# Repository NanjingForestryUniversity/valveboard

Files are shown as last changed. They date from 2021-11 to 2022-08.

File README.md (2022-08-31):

# 阀板

阀板接收上位机给的数据，按其要求控制高速喷阀的开启和关闭，用在棉花、烟叶、茶叶等分选机上，喷阀多用来吹走其中的杂质。因此阀板是分选步骤上控制最终执行机构的驱动板，要求高速、稳定。**这个文件夹下为烟梗分选机阀板相关内容。**

## 目录结构

- 硬件上阀板就是控制喷阀的板子，相关原理图、PCB、BOM、硬件说明等在`hardware`目录里

- 阀板仅驱动喷阀，具体哪个开启哪个关闭要遵循上级的指令，指令传输过程须符合通信协议，通信协议在`protocol`目录里

- 阀板读取通信数据、发出控制信号的操作由阀板上的CPLD进行，其固件和说明见`firmware`目录
- 另外提供了若干输出符合阀板通信协议的信号的例子，在`examples`目录里，严格上这不属于阀板工程

## 版本

由于阀板经常有不同类型的新要求出现，比如24路阀板、32路阀板、控制不同参数的新阀，因此不同的阀板型号（注意不是更新，比如阀板上添加级联接口属于更新）应建立不同的分支，**[b01-c48-ponlytest-vgeneral](https://github.com/NanjingForestryUniversity/valveboard/tree/b01-c48-ponlytest-vgeneral)分支无实际意义**

分支命名规则（不使用中文，小写无空格）

```shell
b分支编号-c路数-p生产环境项目名-v喷阀信息-[-其他特点1[-其他特点2...]]
```

中括号在这里表示可省略的项，中括号本身不应出现在实际命名中，其他特点应字母打头，可有多个，"-"相连

使用Git的tag功能定义版本（注意连着tag一起push），Github仓库的release功能同步发布最新版本的PCB生产文件、PCB制造视图、BOM表、板载固件、通信协议手册

版本号遵循定义如下（不使用中文，小写无空格）

```shell
b分支编号-h硬件版本-p协议版本-f固件版本
```

分支编号和分支命名中编号一致

##  作者

[过奕任](https://github.com/3703781)、丁坤。老阀板工程很乱，重新开发了关于阀板的一切，并放到这个仓库里，以后就在这个仓库里迭代更新。欢迎提[issue](https://github.com/NanjingForestryUniversity/valveboard/issues)，bug随缘解决。

丁坤2019年入学虽然已经毕业，但也很乐意解答关于阀板的所有问题。丁坤QQ1091546069、丁坤电话17761700156。

过奕任2020年入学，目前正打算找其他人接管这个库，毕业了就不要找他，但永远可以找丁坤。

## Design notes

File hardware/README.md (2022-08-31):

# 阀板硬件

这个文件夹下是48路阀板的原理图和PCB，用于烟梗分选机。整个机器用了六块48路阀板，驱动256路喷嘴，阀的型号是合肥旭伟电子气动有限公司的XW-F16，这个阀一个可以连接并控制16个喷嘴。每个阀的电阻是14欧姆，高压启动时峰值电流约1.5A，低压保持电流约0.8A。

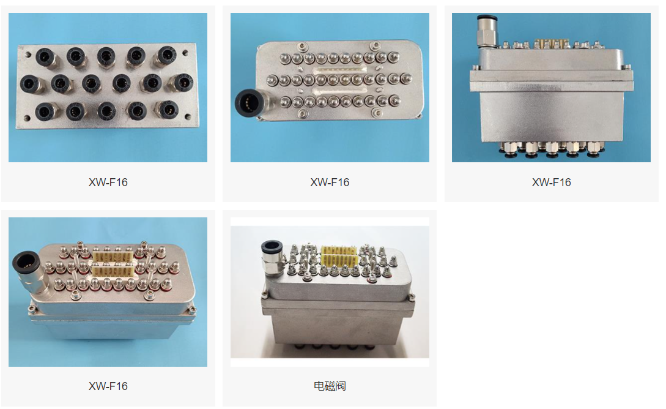
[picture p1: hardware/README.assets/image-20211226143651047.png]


## 概述

48个电磁阀连接在顶部的12个接口上，当接口上有电压时电流流过电磁阀，电磁阀打开。由于电磁阀工作需要大电流大电压且为感性器件，容易影响发出控制信号的CPLD芯片，因此需要独立且隔离的电源，这个电源标为`LOW`，参考为`PGND`。为加快电磁阀开启，在开启瞬间会输出一个高电压，这是另一个独立的电源，标为`HIGH`，参考也为`PGND`。这个高电压会在电磁阀开启后被断开，随后施加标号为`LOW`的保持电压，用来保持电磁阀的打开状态。需要电磁阀关闭则切断保持电压。

上面的过程由光耦隔离驱动端MOS和控制芯片CPLD，提供给光耦输出端的电压标号为`+12V`，参考为`PGND`。

上述提及的`LOW`、`HIGH`、`PGND`、`+12V`仅为板子的丝印上的称呼，都在右上角电源接口输入。

CPLD为控制芯片，接收外部信号并将控制信号输出到板上的光耦，数字电路部分和光耦输入端的电源标号为`DGND`、`+12V`，仅为板子的丝印上的称呼，都在右下角电源接口输入，当然，输入的12V会转换为3.3V提供给数字电路。

设计时是按照下表电压来做的

| 丝印 | 电压 |
| ---- | --- |
| LOW  | 12~24V  |
| HIGH | 24~100V |
| PGND | 0V |
| +12V | 12V |
| DGND | 0V |
| +12V | 12V |

本次所用的阀板加速开启用的高电压为直流100V、保持用的低电压为直流12V

## 调试

**版号**

在`INFO`丝印标志的区域有`S1`、`S2`、`S3`、`S4`标注的0欧电阻焊接位，按`0`、`1`标注焊接即可，注意0和1不能都焊。这个设置是为阀板级联做的冗余。

**烧录**

CPLD烧录口为简牛口，用USB Blaster烧录的，开发软件为Quartus。旁边的按键是复位信号按键，说白了就是复位按键。用`TTL`接口可以方便单端信号的调试

**观察开关量**

在正面那排光耦前有LED，打开的阀门那一路对应的LED亮。选用LED和串联限流电阻时，查看[issue#2](https://github.com/NanjingForestryUniversity/valveboard/issues/2)

**电源**

数字电源输入为12V，在板子上转换为3.3V，网络标号+3.3V，为防止电磁阀上电瞬间直接误动作，因此给光耦电源加入RC延时电路，输出标号为+3.3VGG，按设计延时约500ms，这个时间远大于CPLD初始化开始工作的时间，因此电磁阀上电瞬间不会误动作。此外还添加了防反接保护，查看[issue#3](https://github.com/NanjingForestryUniversity/valveboard/issues/3)

## 生产制造

所需器件BOM里都有，板子开窗部分要加锡，钢网上已经体现了。测试板子是嘉立创做的，SMT也是嘉立创，直插元件和芯片需手焊

## Changelog
### v1.0 

绿色的阀板，测试版本，继承于远古的原理图和布局

### v1.1

蓝色的阀板，过奕任选型和画原理图，丁坤layout，具有ISO、LVDS、TTL接口，见[b01-h1.1-p1.1-f1.1](https://github.com/NanjingForestryUniversity/valveboard/releases/tag/b01-h1.1-p1.1-f1.1)

### v1.2

黄色的阀板，过奕任画原理图和layout，见 [b02-h1.2-p1.1-f1.2](https://github.com/NanjingForestryUniversity/valveboard/releases/tag/b02-h1.2-p1.1-f1.2)

- 采用带屏蔽的超六类RJ45端口代替原来的牛角座，增强了通信的稳定性
- 删除了ISO（隔离）端口
- 删除了LVDS的BYPASS端口
- 删除了TTL端口
- 修改电磁喷阀的接口为更容易买到的器件，[器件详情](https://detail.tmall.com/item.htm?id=633917290163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)
- 增加了光隔数字部分电源的延迟上电电路，避免启动瞬间喷阀动作
- 修改了1N4148的封装为SOD-123，方便SMT
- 略微优化了板子尺寸，调整了安装孔位置和个数

### v1.3

绿色的阀板，过奕任画原理图和layout，见[b02-h1.3-p1.1-f1.3](https://github.com/NanjingForestryUniversity/valveboard/releases/tag/b02-h1.3-p1.1-f1.3)

- 重画了原理图和PCB，PCB尺寸减小
- 增大阻容器件封装，解决100V耐压风险，[issue#1](https://github.com/NanjingForestryUniversity/valveboard/issues/1)
- LED改为黄绿色，[issue#2](https://github.com/NanjingForestryUniversity/valveboard/issues/2)
- 添加了数字电源防反接，[issue#3](https://github.com/NanjingForestryUniversity/valveboard/issues/3)
- 取消了所有保险丝
- 增加了每一路的标识丝印，南林的徽标
- 重新排列了阀的连接器，方便插拔
- 有需要的线路上增加了开窗，提高载流能力

## 作者

[过奕任](https://github.com/3703781)和丁坤一起设计了电路，画了板子。欢迎提[issue](https://github.com/NanjingForestryUniversity/valveboard/issues)，bug随缘解决。

丁坤2019年入学时就被师兄叫去焊接汪学良的阀板，后来和过奕任接替师兄做了这个仓库里的阀板。丁坤已经毕业，但也很乐意解答关于板子的所有问题。丁坤QQ1091546069、丁坤电话17761700156。

过奕任2020年入学，目前正打算找其他人接管这个库，毕业了就不要找他，但永远可以找丁坤。

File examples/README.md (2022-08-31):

# 发送端实现举例

## 概述

按照阀板程序，这里为基于三个平台的发送端实现

- stm32f103

  VScode工程，参考https://github.com/3703781/vstm32code

- zynq7100

  实现了发送模块，可直接例化
  
- epc9600

  基于嵌入式linux的程序，线程安全，具体板子为EPC-9600I-L，是广州致远电子有限公司开发的基于AM335x系列处理器的工控主板，处理器内核为800MHz的Arm Cortex-A8。

##  作者
[过奕任](https://github.com/3703781)、丁坤。欢迎提[issue](https://github.com/NanjingForestryUniversity/valveboard/issues)，bug随缘解决。

过奕任2020年入学，目前正打算找其他人接管这个库，毕业了就不要找他，但永远可以找丁坤。

丁坤2019年入学、丁坤QQ1091546069、丁坤电话17761700156，已经毕业，但很乐意解答所有问题。

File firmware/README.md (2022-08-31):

# 阀板固件

这是阀板上CPLD的固件，严格意义上也属于硬件，因为是描述的硬件结构。这个固件是按照通信协议写的，但比通信协议能适应更广的传输速度，**烟梗分选机上`SCLK`为2MHz，高电平时间为0.2ms**

## 如何烧录

Quartus软件

## 程序说明

看程序注释

## Changelog
### v1.0

继承自老程序

### v1.1

丁坤重写了

### v1.2

修正了引脚分配

### v1.3

- 添加了高电压抑制，见[issue#4](https://github.com/NanjingForestryUniversity/valveboard/issues/4)
- 修正了高电压时间为0.2ms

### v1.4

确认了阀不需要长时间开启保护，删除了阀板固件v1.4-beta1([commit 6af8df](https://github.com/NanjingForestryUniversity/valveboard/commit/6af8dfd09c268d677a46063cc9637f573e69919e))中的长时间开启保护，见[issue#6](https://github.com/NanjingForestryUniversity/valveboard/issues/6)

## 作者
[过奕任](https://github.com/3703781)、丁坤

过奕任自师兄王聪（2018年入学）毕业后硬件方面师门出现空档期，被老倪催的没办法了，就学了硬件并顺手写了这份FPGA代码。丁坤是专门搞嵌入式的，但也看过这份代码。欢迎提[issue](https://github.com/NanjingForestryUniversity/valveboard/issues)，bug随缘解决。

过奕任2020年入学，目前正打算找其他人接管这个库，毕业了就不要找他，但永远可以找丁坤。

丁坤2019年入学、丁坤QQ1091546069、丁坤电话17761700156，已经毕业，但很乐意解答所有问题。

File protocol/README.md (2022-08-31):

# 阀板通信协议

## 概述

由6条差分信号`SCLK+`,`SCLK-`,`SEN+`,`SEN-`,`SDATA+`,`SDATA-`

显然共计3个信号

- `SCLK`为1MHz同步时钟，周期抖动小于500ps
- `SEN`为传输状态
- `SDATA`为阀控制信号，1表示关，0表示开，小端模式

## 物理层

- LVDS差分

- 灰色排线

## 数据链路层

jkl

当需要传输一帧数据时，首先在`SCLK`的一个下降沿拉高`SEN`并建立第一个阀的控制信号V0，接收电路将在`SCLK`上升沿采样。n表示通道数，即所需控制阀门的数量，整个传输过程中，须将`SEN`拉高保持n个`SCLK`周期，期间发送n个`SDATA`阀控制信号，分别对应第1个到第n个阀。待最后一个阀的控制信号发送完成后，在`SCLK`到达下一个下降沿时，拉低`SEN`。

在两帧的间隔中，应持续保持发送1MHz的`SCLK`，接收端将通过`SCLK`的电平跳转来判断是否断开连接。另外，两帧数据的间隔应至少为5个`SCLK`周期。 

| Symbol | Parameter | Min  | Typ  | Max  | Unit |
| --- | --- | ---- | ---- | ---- | ---- |
| t1 | SCLK setup time | 250  | 500  | 750  | ns |
| t2 | Data output access time  | - | 250  | 280  | ns |
| t3 | SEN hold time | 250  | 500  | 750  | ns |
| t4 | Data output disable time | - | 250  | 280  | ns |

*Condition at SCLK=1MHz

下面是每一位数据的具体时序

jkl2

| Symbol | Parameter | Min  | Typ  | Max  | Unit |
| --- | --- | ---- | ---- | ---- | ---- |
| t5 | Data output valid time | 50** | 500  | 750  | ns |
| t6 | Data output hold time  | 250  | 500  | 750  | ns |

*Condition at SCLK=1MHz
**Limit value

发送端须同时满足`t1`~`t5`的参数要求

## 电路

DS90LV048具有内置终端电阻，电路设计和布局布线只需注意匹配100欧姆差分阻抗

接收端

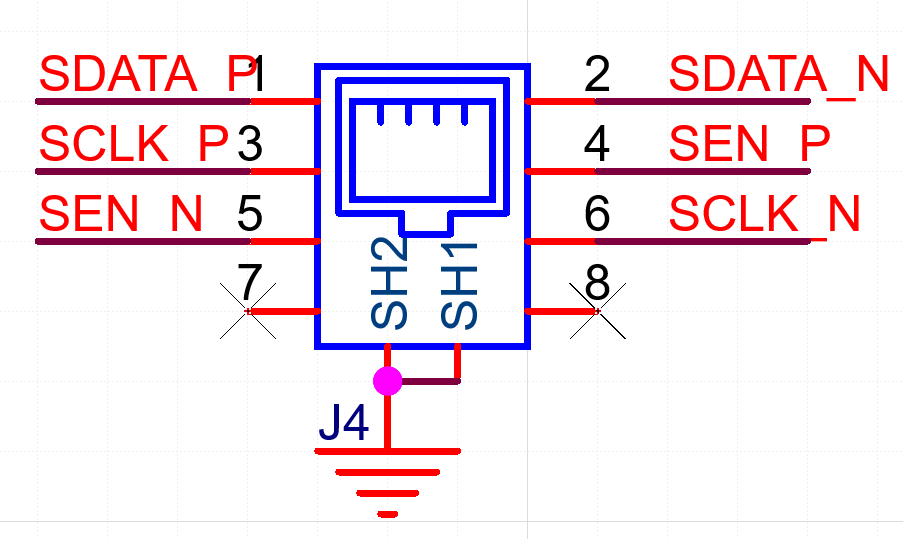
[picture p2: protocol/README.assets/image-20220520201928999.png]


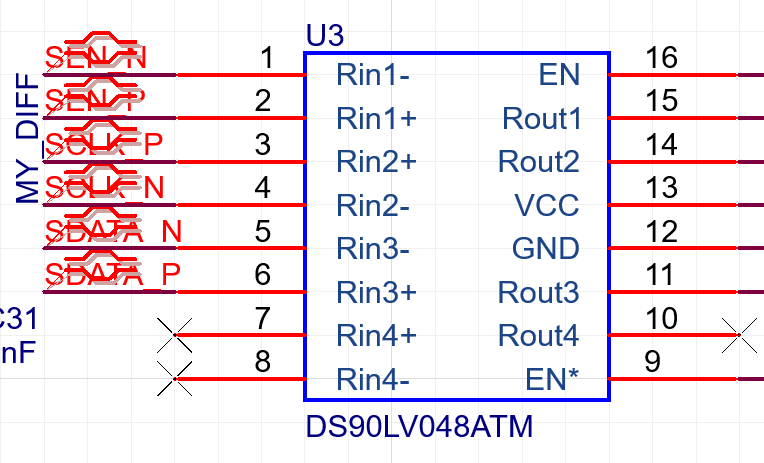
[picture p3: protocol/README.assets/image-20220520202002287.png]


发送端

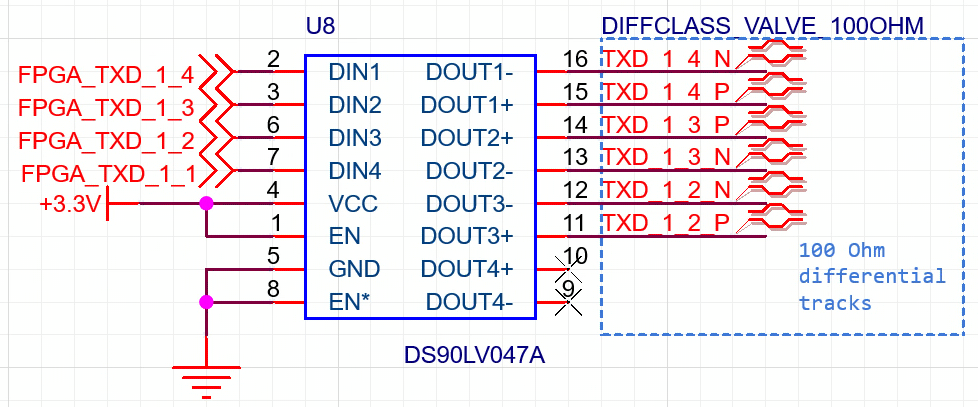
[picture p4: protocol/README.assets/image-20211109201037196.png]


##  作者
[过奕任](https://github.com/3703781)、丁坤。老阀板的协议不明确（其实就没有协议，逆向工程后改进出来的这份协议），所以就大概描述了一下协议相关信息。欢迎提[issue](https://github.com/NanjingForestryUniversity/valveboard/issues)，bug随缘解决。

过奕任2020年入学，目前正打算找其他人接管这个库，毕业了就不要找他，但永远可以找丁坤。

丁坤2019年入学虽然已经毕业，但也很乐意解答关于这份协议的所有问题。丁坤QQ1091546069、丁坤电话17761700156。

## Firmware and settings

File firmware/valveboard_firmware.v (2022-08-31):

/* 
阀板程序v1.4 2022/8/31
经测试，高压时间改为0.2ms
使用的是合肥的阀，1.5A电流需0.2ms的100V(阀标称100V，现场供电为96V)高电压
*/

module valveboard_firmware(
			input sys_clk,  // 20MHz
			input rst_n,
			input line_sclk,
			input line_sen,
			input line_sdata,
			
			output reg [47:0]  signal_high_voltage,
			output reg [47:0]  signal_low_voltage
			
		);
		
	parameter CHANNEL_NUM = 48;
	parameter CHANNEL_NUM_MINUS_1 = CHANNEL_NUM - 1;
	parameter HIGH_VOLTAGE_TIME = 32'd4000;  // 高压时间HIGH_VOLTAGE_TIME / 20MHz = 0.2ms
	parameter HIGH_VOLTAGE_TIME_MINUS_1 = HIGH_VOLTAGE_TIME - 1;
	parameter FAULT_COUNTER_THRESHOLD = 32'd20_000_000;  // 通讯中断超过FAULT_COUNTER_THRESHOLD / 20MHz = 200ms，就关所有阀
	parameter FAULT_COUNTER_THRESHOLD_MINUS_1 = FAULT_COUNTER_THRESHOLD - 1;
	parameter FAULT_COUNTER_THRESHOLD_PLUS_1 = FAULT_COUNTER_THRESHOLD + 1;
	
		
	
	reg [CHANNEL_NUM_MINUS_1:0] cache_signal_high_voltage;
	reg [31:0] i;
	reg [31:0] fault_counter;
	reg [0:0] fault_flag [0:7];  // fault_flag支持8类错误信号
	
	
	/**
	 * 维护错误信号
	 */
	wire total_fault_flag = fault_flag[7] | fault_flag[6] | fault_flag[5] | fault_flag[4] | fault_flag[3] | fault_flag[2] | fault_flag[1] | fault_flag[0];
	integer j;
	initial begin
	  for (j = 0; j < 8; j = j + 1) begin
		fault_flag[j] = 1'b0;
	  end
	end
//	/**
//	 * 产生周期为100kHz的posedge_100khz信号，信号高电平持续1个sys_clk
//	 */
//	reg[7:0] cnt_for_posedge_100khz;
//	reg posedge_100khz;
//	always @(posedge sys_clk or negedge rst_n) begin
//		if(!rst_n) begin
//		   cnt_for_posedge_100khz <= 0;
//		end
//		else if(cnt_for_posedge_100khz == 199) begin
//			posedge_100khz <= 1;
//			cnt_for_posedge_100khz <= 0;
//		end
//		else begin
//			cnt_for_posedge_100khz <= cnt_for_posedge_100khz + 1;
//			posedge_100khz <= 0;
//		end                            
//	end

	/**
	 * 在输入的line_sclk信号上升沿产生1个sys_clk时长高电平的脉冲信号posedge_line_sclk，比原信号延迟(4,5]个sys_clk
	 */
	reg [4:0] cache_line_sclk;
	reg posedge_line_sclk;
	always@(posedge sys_clk or negedge rst_n) begin
		if (!rst_n) begin
			cache_line_sclk <= 0;	
			posedge_line_sclk <= 0;
		end
		else begin
			cache_line_sclk <= {cache_line_sclk[3:0], line_sclk};
			if ({cache_line_sclk, line_sclk} == 6'b011111)
				posedge_line_sclk <= 1;
			else
				posedge_line_sclk <= 0;
		end
	end
	
	/**
	 * filter_line_sdata比原信号延迟(4,5]个sys_clk
	 */
	reg [4:0] tmp_cache_line_sdata;
	reg fiter_line_sdata;
	always@(posedge sys_clk or negedge rst_n) begin
		if (!rst_n) begin
			tmp_cache_line_sdata <= ~0;
		end
		else begin
			tmp_cache_line_sdata <= {tmp_cache_line_sdata[3:0], line_sdata};
			fiter_line_sdata <= tmp_cache_line_sdata[4];
		end
	end
	
	/**
	 * 在输入的line_sen信号上升沿产生1个sys_clk时长高电平的脉冲信号posedge_line_sen，比原信号延迟(4,5]个sys_clk
	 * 在输入的line_sen信号下降沿产生1个sys_clk时长高电平的脉冲信号negedge_line_sen，比原信号延迟(4,5]个sys_clk
	 * 缓存和整理line_sen信号得filter_line_sen，比原信号延迟(4,5]个sys_clk
	 */
	reg [4:0] cache_line_sen;
//	reg posedge_line_sen;
	reg filter_line_sen;
	reg negedge_line_sen;
	always@(posedge sys_clk or negedge rst_n) begin
		if (!rst_n) begin
			cache_line_sen <= 0;
			filter_line_sen <= 0;
//			posedge_line_sen <= 0;
		end
		else begin
			cache_line_sen <= {cache_line_sen[3:0], line_sen};
			if ({cache_line_sen, line_sen} == 6'b011111) begin
//				posedge_line_sen <= 1;
				filter_line_sen <= 1;
				negedge_line_sen <= 0;
			end
			else if ({cache_line_sen, line_sen} == 6'b100000) begin
//				posedge_line_sen <= 0;
				filter_line_sen <= 0;
				negedge_line_sen <= 1;
			end
			else begin
//				posedge_line_sen <= 0;
				filter_line_sen <= filter_line_sen;
				negedge_line_sen <= 0;
			end
		end
	end
	
	/**
	 * line_clk上升沿采样line_sdata，采样时刻与posedge_line_sclk下降沿对齐
	 * total_fault_flag会相对line_clk异步结束本次通信
	 * recv_complete指示是否接收完成，单sys_clk周期宽度，与negedge_line_sen信号对齐
	 */
	reg [CHANNEL_NUM_MINUS_1:0] cache_line_sdata;
	wire recv_complete = negedge_line_sen && (i == CHANNEL_NUM);
	always @ (posedge sys_clk or negedge rst_n) begin
		if (!rst_n) begin
			i <= 0;
			cache_line_sdata <= ~0;
		end
		else if (total_fault_flag) begin
			i <= 0;
			cache_line_sdata <= ~0;
		end
		else if (filter_line_sen && posedge_line_sclk) begin
			cache_line_sdata[i] <= fiter_line_sdata; 
			i <= i + 1;  
		end
		else if (negedge_line_sen) begin
			i <= 0;
		end
	end
	
	/**
	 * 若接收超过CHANNEL_NUM个数据，产生错误信号fault_flag[0]；fault_flag[0]将在posedge_line_sen上升沿时刻清楚
	 */
	always @ (posedge sys_clk or negedge rst_n) begin
		if (!rst_n)
			fault_flag[0] <= 0;
		else if (i > CHANNEL_NUM)
			fault_flag[0] <= 1;
		else if ({cache_line_sen, line_sen} == 6'b011111)
			fault_flag[0] <= 0;
		else
			fault_flag[0] <= fault_flag[0];
	end
	 
	/**
	 * 若通讯中断，超过FAULT_COUNTER_THRESHOLD个csys_clk就置位fault_flag[1]
	 * fault_flag[1]在posedge_line_sclk上升沿时刻清楚
	 */
	always @(posedge sys_clk or negedge rst_n) begin
		if (!rst_n) begin
			fault_counter <= 0;
			fault_flag[1] <= 0;
		end
		else if ({cache_line_sclk, line_sclk} == 6'b011111) begin
			fault_counter <= 0;
			fault_flag[1] <= 0;
		end
		else begin
			if (fault_counter >= FAULT_COUNTER_THRESHOLD_PLUS_1)
				fault_flag[1] <= 1;
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

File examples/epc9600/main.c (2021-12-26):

#include <valve.h>
#include <sys/socket.h>
#include <arpa/inet.h>
#include <math.h>

queue_msg_t queue_msg = {NULL, 1024, 0, 0, 0, 0, 0};
valvedata_t valvedata = {0};
queue_msg_t queue = {0};

#define ROTATE_UINT64_RIGHT(x, n) ((x) >> (n)) | ((x) << ((64) - (n)))
#define ROTATE_UINT64_LEFT(x, n) ((x) << (n)) | ((x) >> ((64) - (n)))

int main(int argc, char *argv[])
{
    uint64_t aaa = (uint64_t)pow(2.0, 48.0);
    printf(motd);
    queue_init(&queue, 1024);
    valve_init();
    valvedata.valvedata_1 = 1;
    for (uint64_t i = 0; i < aaa; i++)
    {
        valvedata.valvedata_1 = i;  // ROTATE_UINT64_RIGHT(valvedata.valvedata_1, 1);
        valve_sendmsg(&valvedata);
    }
    queue_deinit(&queue);
    valve_deinit();
    printf(motd2);
    return 0;
}

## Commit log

2021-11-21 init branch
    [VALVEBOARD_DigitalPower_DigitalInterface_Controller.SchDoc, VALVEBOARD_Isolation.SchDoc, VALVEBOARD_ValveDrive1.SchDoc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]
2022-05-20 v1.2 version on tobaccosorting
    hardware: change IDC connector to RJ45 with shield, communicate with CAT6E network cable remove some unnecessary ports
    [VALVEBOARD_DigitalPower_DigitalInterface_Controller.SchDoc, VALVEBOARD_Isolation.SchDoc, VALVEBOARD_ValveDrive1.SchDoc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]
2022-05-26 fix pin assignment
    pin 39, 40, 41 order was wrong, which makes it failed to communicate with lower machine
2022-07-26 整理了原理图 修改了PCB
    1. 添加了防反接电路
    2. 删除了保险丝
    3. 增大了喷阀走线载流能力
    [VALVEBOARD_Controller.SchDoc, VALVEBOARD_DigitalInterface.SchDoc, VALVEBOARD_DigitalPower.SchDoc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]
2022-08-24 固件中添加了高电压抑制
    如果阀已经是开的，就不再施加加速开启的高电压
    [ValveBoard_bom_v1.3.xlsx, ValveBoard_pnp_v1.3.csv, bom.xlsx]
2022-08-24 每路阀添加单独的开启超时机制
    改动了固件
2022-08-31 确认了不需要长时间开启保护 issue#6
2022-08-31 更新了版本说明
